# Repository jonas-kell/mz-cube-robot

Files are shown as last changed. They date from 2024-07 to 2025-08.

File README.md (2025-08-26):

# Mathezirkel-Cube-Solving-Robot

https://github.com/user-attachments/assets/eca1f05e-32c8-4683-82ac-e17c1d3a330d

<table style="width: 100%; border-collapse: collapse; border: none;">
    <tr>
        <td style="text-align: center; vertical-align: middle;">
            <video src='files/VideoDemonstration.mp4' controls loop autoplay style="max-width: 45vw; max-height: 80vh;"></video>
        </td>
        <td style="text-align: center; vertical-align: middle;">
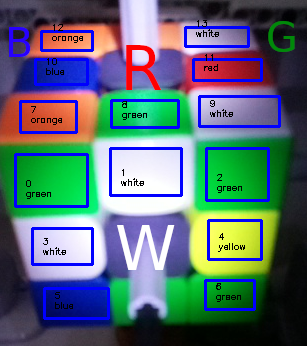
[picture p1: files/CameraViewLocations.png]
            
        </td>
    </tr>
</table>
  
## What is this

This is a Project, undertaken first at the `Mathecamp` of the `University of Augsburg` 2024.
The idea is to

-   Develop a Robot from scratch, that can solve the `Rubics-Cube` without external inputs
-   Make this experience as teachable as possible for young students, that might or might not have been working with robotics/coding yet

## How is this realized

A first version was made to work in September 2024. Videos of the Results can be seen above ([or HERE](https://github.com/user-attachments/assets/eca1f05e-32c8-4683-82ac-e17c1d3a330d)).

The code and Hardware-Setup that is needed to get this working is fully contained in this repository.

There is a list of materials and how to do the basic setup [here](/setup-configuration/bill-of-materials.md).

A Lego-building instruction however is NOT contained here. Though the video can be taken as reference.

Basically, he robot is comprised of a `Raspberry-Pi Zero W` with a camera module.
It provides the stream of the camera view over a simple webserver.
It also relays motor commands to two `Lego Ev3` bricks, that control in total 6 motors, one for each face of the cube.

The `Raspberry-Pi Zero W` has its Wireless capabilities configured as an access point.
One can then connect to that access point and run code one ones own Laptop that processes the camera stream and issues the rotation commands, until the cube is solved.

## What to find in this repository

-   [Bill of Materials](setup-configuration/bill-of-materials.md)
-   [Hardware configuration](setup-configuration/hardware-configuration.md)
-   [Installation instructions](setup-configuration/installation-instructions.md)
-   [Startup instructions for when everything is installed](setup-configuration/startup.md)
-   [Server code to run on the Raspberry Pi](rpi-server.py)
-   [Server code to run on the EV3s](ev3-server.py)
-   [A possible set of processing and issuing functions](solving-example-code/)

## Gallery

The photos are also found at their respective locations in the sub-modules of the explanation above.

<table style="width: 100%; border-collapse: collapse; border: none;">
    <tr>
        <td style="text-align: center; vertical-align: middle;">
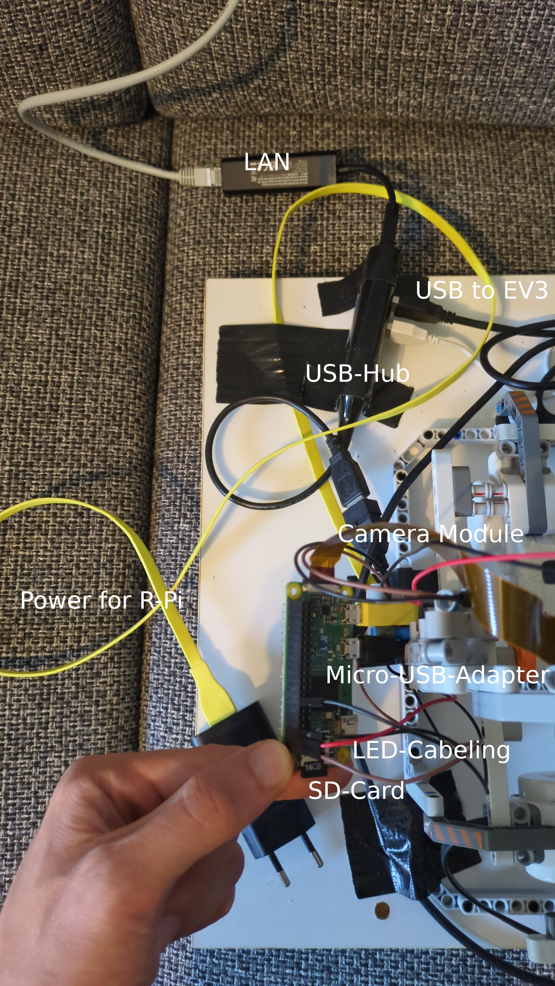
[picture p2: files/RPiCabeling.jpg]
            
        </td>
        <td style="text-align: center; vertical-align: middle;">
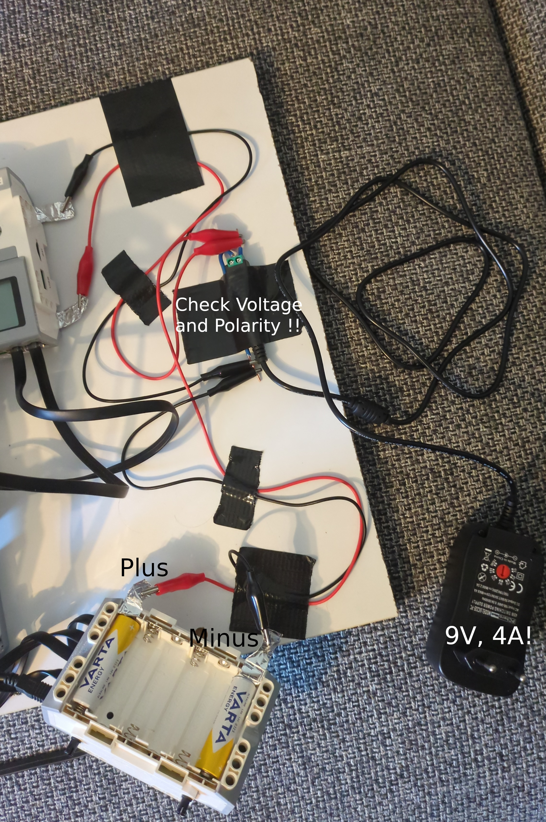
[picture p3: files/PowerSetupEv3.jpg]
            
        </td>
    </tr>
</table>
<table style="width: 100%; border-collapse: collapse; border: none;">
    <tr>
        <td style="text-align: center; vertical-align: middle;">
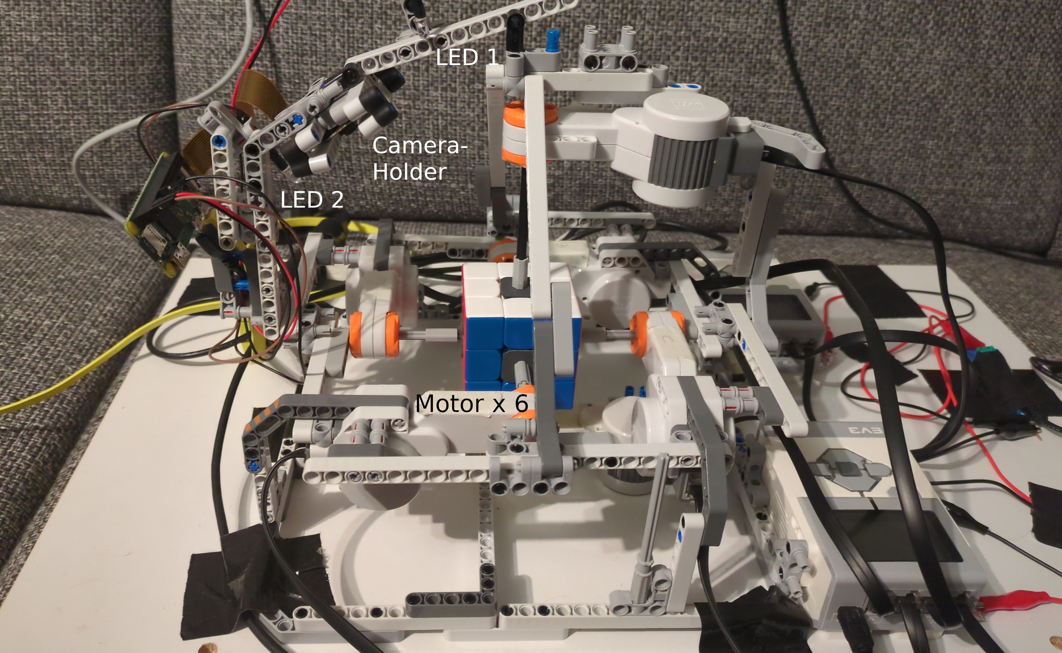
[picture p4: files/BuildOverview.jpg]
            
        </td>
    </tr>
</table>
<table style="width: 100%; border-collapse: collapse; border: none;">
    <tr>
        <td style="text-align: center; vertical-align: middle;">
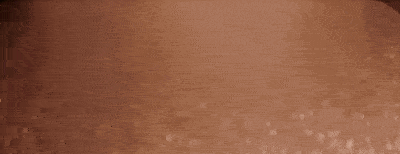
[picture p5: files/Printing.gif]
            
        </td>
        <td style="text-align: center; vertical-align: middle;">
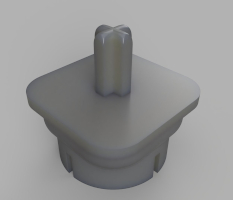
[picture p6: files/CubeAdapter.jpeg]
            
        </td>
    </tr>
</table>

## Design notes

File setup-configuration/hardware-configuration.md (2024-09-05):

# Hardware Configuration

How to setup the hardware:

## Raspberry Pi Setup

-   Connect the Power-Port with the Micro-USB Cable to the 5V Power-Supply
-   Connect the Data-Port to the Micro-USB to USB-A-female Adapter and plug the USB-Hub into this.
    -   Into this, you plug the USB-A sides of the cables that lead to the `Lego EV3`s
    -   Optional: USB-A to ethernet adapter to have LAN-Connectivity to the contraption
-   Get the LEDs to shine with the resistor and the jumper wires (breadboards or soldering required) ([Tutorial](https://www.elektronik-kompendium.de/sites/raspberry-pi/2102181.htm))
    -   [Pinout of the raspberry pi zero](https://pinout.xyz/pinout/io_pi_zero)
        -   I used 2,4 for one side and 6,14 for the other (check polarity of LED)
-   Flash the OS to one of the micro SD-Cards
    -   [Tutorial, to follow for Camera Setup](https://www.conrad.de/de/ratgeber/schule-unterricht/raspberry-pi/ueberwachungskamera-mit-raspberry-pi.html)
    -   [Flashing Program: Raspberry Pi Imager](https://www.raspberrypi.com/software/)
        -   When Flashing the os, make sure to `enable ssh` and set password to `pi`
        -   [Which OS?](https://www.raspberrypi.com/software/operating-systems/)
            -   Raspberry Pi OS (other)
                -   Raspberry Pi OS (Legacy - 32 bit) Lite
    -   Insert into the SD-Card Slot
-   Connect the camera module to the raspberry Pi Zero

## EV3 Setup (Both completely the same)

-   Power Management
    -   Either load with 6AA batteries each
    -   OR connect 9V Wall brick to the power terminals
        -   best to get a connection to the terminal, by wedging Aluminum-Foil/Tinfoil onto the contacts with one AA battery
            -   (the battery just has the correct size, will not be part of the circuit, may also be an empty one)
            -   Check Polarity and which terminal to use
            -   Best to use a Multimeter to check Voltage (9V) and Polarity (see image)
            -   Power supply should provide 4A, lower specs may result in the brick shutting down under load
-   Flash the [ev3dev](https://www.ev3dev.org/docs/getting-started/) onto the remaining two SD-Cards
    -   Can also use Raspberry Pi Imager for this task
    -   Insert the SD-Cards into the `Lego EV3` slot
-   Connect the USB-Cables to the USB-Hub (keep the connection, generally the same configuration. Swapping them may break the assignment in the Network Manager, later)
-   Build your Model (Requires your creativity and a lot of Lego-Parts)
    -   Your freedom of design choice.
        -   Should connect one motor to every face of the cube
        -   Motors should spin freely, the cube nicely in the center
            -   Probably best, to have opposite face motors on the same ev3, as they turn together posssibly
            -   I chose the configuration (See directions on picture below):
                -   A - Blue - Motor Port A, EV3 1
                -   B - Green - Motor Port B, EV3 1
                -   C - Orange - Motor Port C, EV3 1
                -   D - Red - Motor Port D, EV3 1
                -   E - White - Motor Port A, EV3 2
                -   F - Yellow - Motor Port A, EV3 2
        -   Space for the camera to view at least two sides of the cube (the more you can easily see, the easier the detection)
        -   Mount the LEDs, so that they can be powered and still illuminate the cube faces nicely

<table style="width: 100%; border-collapse: collapse; border: none;">
    <tr>
        <td style="text-align: center; vertical-align: middle;">
            
        </td>
        <td style="text-align: center; vertical-align: middle;">
            
        </td>
    </tr>
</table>
<table style="width: 100%; border-collapse: collapse; border: none;">
    <tr>
        <td style="text-align: center; vertical-align: middle;">
            
        </td>
    </tr>
</table>

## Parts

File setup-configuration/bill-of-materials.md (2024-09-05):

# Bill of Materials

What is required to reproduce this setup

-   Two `Lego EV3` ([Discontinued](https://www.lego.com/de-lu/product/lego-mindstorms-ev3-31313), go to ebay)
    -   Six Motors (When you have two EV3, you get 4 large and 2 small motors. The small ones have a different speed though. I happen to have 6 `Lego NXT 2.0 - Motors`).
-   One `Raspberry Pi Zero W` (Zero 2 probably also works and is more performant) [Like this](https://www.reichelt.de/raspberry-pi-zero-w-v-1-1-1-ghz-512-mb-ram-wlan-bt-rasp-pi-zero-w-p256438.html)
    -   `Camera Module` for the Raspberry Pi [Like this](https://www.reichelt.de/raspberry-pi-kamera-8mp-67-v2-rasp-cam-2-p170853.html)
    -   `Pi Zero compatible Adapter Flex Cable` (smaller pins on one side!!) [Like this](https://www.reichelt.de/raspberry-pi-zero-flexkabel-fuer-standard-kameramodul-15cm-rpiz-cam-fl15-p223615.html)
-   Three `16 Gb Micro-SD-Cards` (One for the RPi, one for each of the two EV3)
-   One `Micro USB to USB-A female Adapter` ([Like this](https://www.reichelt.de/de/de/raspberry-pi-kabel-micro-usb-m-auf-usb-typ-a-f-otg-10cm--rpi-usb-b-a-1-wt-p316284.html))
-   One `USB-A USB-Hub` (ideally powered) ([Like this](https://www.reichelt.de/usb-2-0-4-port-hub-4x-a-equip-128955-p311104.html))
-   One `Micro USB to USB-A cable` to power the Raspberry Pi ([Like this](https://www.reichelt.de/usb-2-0-kabel-a-stecker-auf-micro-b-stecker-3-m-shvp-77183-w-p211162.html))
    -   USB-A power brick (Basically any does) ([Like this](https://www.reichelt.de/usb-ladegeraet-5-v-1000-ma-schwarz-goobay-44947-p265655.html))
-   For the LED-Lighting
    -   2x (or more) White LEDs ([Like these](https://www.reichelt.de/led-5-mm-bedrahtet-kaltweiss-18000-mcd-15--led-5-18000-ws-p76715.html))
    -   Cables to solder and connect ([Like these](https://www.reichelt.de/entwicklerboards-steckbrueckenkabel-40-pole-m-m-40-cm-debo-kabelset22-p340347.html))
    -   2x 100 Ohm Resistor (To avoid burning out the LED, when connected to 5V of Pi Zero, [LED Calculator](https://www.digikey.de/de/resources/conversion-calculators/conversion-calculator-led-series-resistor)) ([Like these](https://www.reichelt.de/widerstand-metalloxyd-100-ohm-0207-1-0-w-5--1w-100-p1777.html))
-   If you want to power the `Lego EV3` over Wall power (not feed it 100s of batteries)
    -   Wall power supply, that does 9-10V ([Like this](https://www.amazon.de/dp/B0CCV95BSF))
    -   Alligator Clips ([Like these](https://www.amazon.de/dp/B0D7V5G3WT))
    -   4 Batteries, Tinfoil
    -   Some wire parts, pliers, soldering iron and stuff for connecting them
-   A Rubics-Cube that can have the center caps removed ([This one probably fits the printed adapters](https://speedcubeshop.com/products/moyu-rs3-m-2020-3x3-magnetic))

    -   6 Adapters to connect the YOUR Rubics-Cube centers to Lego-Axles (3d-Printing required or other alternative you fancy, e.g. some hardening putty or what do I know)
    -   [.stl File of the Adapter Model used](./../files/CubeAdapter.stl). Thanks to [@jangeiger](https://github.com/jangeiger) for designing and printing :-)

        Printing &nbsp;&nbsp;&nbsp;&nbsp;&nbsp;&nbsp;&nbsp;&nbsp;&nbsp; Adapter

## Legacy/Alternatives

this project was initially envisioned to be working with one `Lego EV3` and one `Lego NXT 2.0`.
Alternatively two `Lego NXT 2.0`.

The problem is, that one of either `Lego EV3` or `Lego NXT 2.0` doesn't have enough motor-ports for controlling 6 motors.

There is a non-complete version for using `Lego NXT 2.0`.
For one, an old version of the server scripts can be found in the history: [COMMIT](https://github.com/jonas-kell/mz-cube-robot/blob/22c137ebf0f76d9267865a2a87c0837d4efc5210/rpi-server.py).

Also configuration files and other resources are in [this legacy folder](../testing-preparation-setup/nxt-slave/).

This was scrapped due to not solvable motor precision errors when using `Lego NXT 2.0`.

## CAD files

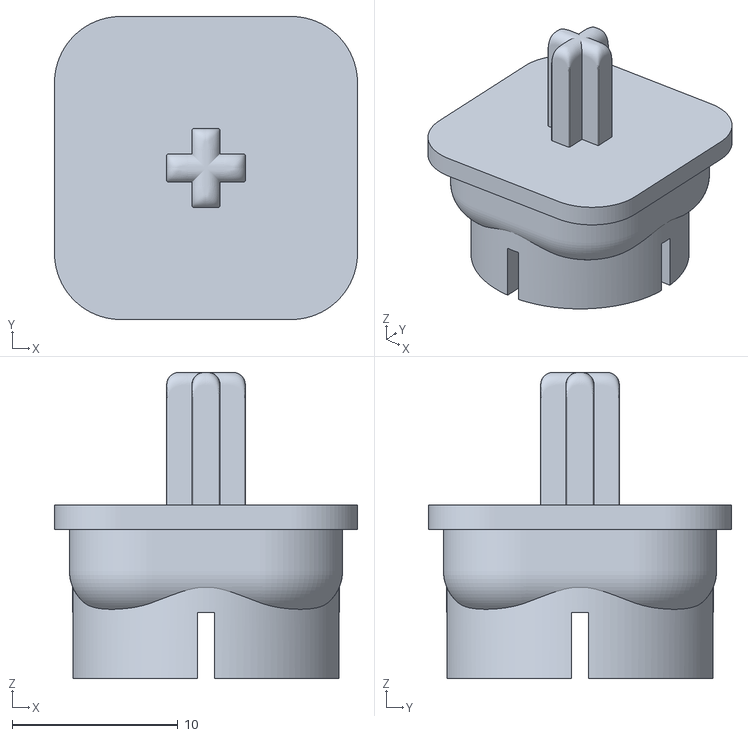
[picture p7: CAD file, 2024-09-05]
files/CubeAdapter.stl
18.3 x 18.3 x 18.5

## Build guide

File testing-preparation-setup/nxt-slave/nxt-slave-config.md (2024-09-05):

# Legacy: talk to NXT2.0

[Last commit, where this was used](https://github.com/jonas-kell/mz-cube-robot/blob/22c137ebf0f76d9267865a2a87c0837d4efc5210/rpi-server.py).

This was scrapped due to not solvable motor precision errors when using `Lego NXT 2.0`.

```shell
# required installations on the raspberry pi zero w to get the nxt-communication package to work
pip install --upgrade pip
pip install --upgrade nxt-python
pip install --upgrade pyusb
```

It was tried, to make this run on the `Lego EV3`, as it has a USB-Host port and could control the `Lego NXT 2.0`.
This was however unsuccessful, to the python version in [ev3dev](https://www.ev3dev.org/) and the requirement for the control pip lib [nxt-python](https://github.com/schodet/nxt-python).

Therefor, the `Raspberry Pi Zero W` was chosen to issue the commands to the `Lego NXT 2.0`.

-   [Main test](discover.py)

Direct Control (running motors commands directly over USB) is way to imprecise.
This is because the device reading the motor encoder and issuing start/stop is incapable to do so effectively due to the USB-delay.

-   [Direct Control EV3](ev3_slave.py)
-   [Direct Control NXT](nxt_slave.py)

The "solution" that reduced that problem, was to run code locally on the `Lego NXT 2.0` that turns the motors and only communicate the direction/speed/amount over serial communication, eliminating the inaccuracy.

The programs were written in [Open Roberta Lab](https://lab.open-roberta.org/), as this is a nice - still supported - way to program the legacy `Lego NXT 2.0`.

The setup how to talk to the robot was under the `Open Roberta Wiki` under `»Set Up«`. This has moved to a confluence site with required login, since, so I refuse to write down links to the details now...

The programs that used the bluetooth communication api to read the message how far and which motor to turn are [Here](./messagemotor.xml).
Attempts were made, to [run motors in parallel](./messagemotorparallel.xml) that were fully unsuccessful.

[Some example how to write messages (text/numbers)](./message.py) to the `Lego NXT 2.0`.

[This server implementation](https://github.com/jonas-kell/mz-cube-robot/blob/22c137ebf0f76d9267865a2a87c0837d4efc5210/rpi-server.py) used a second message channel that was checked for message box empty-nes, because writing messages back into the box from nxt was unsuccessful and so this was the only way I fond to communicate back to the server that we are done.

## END

In the end still motor positioning of any of these was not sufficiently precise enough for repeated use in the final application.

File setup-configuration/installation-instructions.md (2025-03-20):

# Installation Instructions

## On the HOST-Computer (Laptop or whatever processes the image stream and sends the commands)

-   Install the [VS-code ev3-dev extension](https://marketplace.visualstudio.com/items?itemName=ev3dev.ev3dev-browser) if you want to interface directly with the ev3s (like for uploading files, when no network configuration up, yet).
-   Install the [VS-code Python extension](https://marketplace.visualstudio.com/items?itemName=ms-python.python)
-   Python Extensions (in a proper `venv`, not globally):

    ```shell
    python3 -m venv .venv
    source .venv/bin/activate

    pip install --upgrade pip
    pip install --upgrade python-ev3dev2
    pip install --upgrade opencv-python
    pip install --upgrade scikit-image
    pip install --upgrade RubikTwoPhase

    ------ to deactivate
    deactivate
    ```

## On the `Raspberry Pi Zero W`

-   When Flashing the os, MAKE SURE to `enable ssh` and set password to `pi` (otherwise, you will not be able to connect to it, if you do not happen o have the proper HDMI-accessories)
-   Source code initially taken from the [official PiCamera package](http://picamera.readthedocs.io/en/latest/recipes2.html#web-streaming)
-   Make sure, the files are copied onto the devices
    -   [rpi-server](./../rpi-server.py) onto the Raspberry PI with the top level folder `mz-cube-robot`
-   Enable Camera Support

    ```shell
    sudo raspi-config
    ```

    -   Interface Options
        -   Legacy Camera support
            -   Enable
    -   RESTART

-   Install packages

    ```
    sudo apt install python3-picamera
    export PATH="/home/pi/.local/lib/python3.9/site-packages:$PATH"

    # to solve on the pi
    sudo apt-get install python3-opencv
    sudo apt-get install python3-skimage
    sudo pip3 install --upgrade RubikTwoPhase --default-timeout=100

    ```

-   Make the wlan interface be an Access-Point to connect to

    -   Settings to generate a Access-Point with `SSID = CUBEROBOTWLAN` and `Password = cuberobot`

        -   In that network, the `Raspberry Pi Zero W` will have the ip `192.168.1.1`, meaning, the website will be available under [http://192.168.1.1/](http://192.168.1.1/)

    -   Install Packages

    ```shell
    sudo apt install dnsmasq hostapd iptables
    ```

    -   Edit the configuration

    ```shell
    sudo nano /etc/dhcpcd.conf

    >>>>>

    interface wlan0
    static ip_address=192.168.1.1/24
    nohook wpa_supplicant
    ```

    ```shell
    sudo mv /etc/dnsmasq.conf /etc/dnsmasq.conf_alt
    sudo nano /etc/dnsmasq.conf

    >>>>>

    # DHCP-Server active for WLAN-Interface
    interface=wlan0
    # DHCP-Server not active for other networks
    no-dhcp-interface=eth0
    # IPv4-Address-Range and Lease-Time
    dhcp-range=192.168.1.100,192.168.1.200,255.255.255.0,24h
    # DNS - We
    dhcp-option=option:dns-server,192.168.1.1
    ```

    ```shell
    sudo nano /etc/hostapd/hostapd.conf

    >>>>>

    ### WLAN-Access-Point-Mode

    # Interface and driver
    interface=wlan0
    # driver=nl80211 # Commented out, may be necessary

    # WLAN-Configuration
    ssid=CUBEROBOTWLAN
    channel=1
    hw_mode=g
    ieee80211n=1
    ieee80211d=1
    country_code=DE
    wmm_enabled=1

    # WLAN-Encryption
    auth_algs=1
    wpa=2
    wpa_key_mgmt=WPA-PSK
    rsn_pairwise=CCMP
    wpa_passphrase=cuberobot
    ```

    ```shell
    sudo nano /etc/default/hostapd

    >>>>>

    RUN_DAEMON=yes
    DAEMON_CONF="/etc/hostapd/hostapd.conf"
    ```

    -   Start Service (Probably best to also reboot and see if it still works)
        -   !!! If you broke network config, you may no longer be able to connect to the device at all

    ```shell
    sudo systemctl unmask hostapd
    sudo systemctl start hostapd
    sudo systemctl enable hostapd
    ```

-   (Optional) Set the program to autostart:

    ```shell
    sudo nano /etc/systemd/system/controlserver.service
    ```

    ```conf
    [Unit]
    Description=Cube solver control server
    After=network.target

    [Service]
    User=root
    WorkingDirectory=/home/pi/mz-cube-robot
    ExecStart=/usr/bin/python3 /home/pi/mz-cube-robot/rpi-server.py
    Restart=always

    [Install]
    WantedBy=multi-user.target
    ```

    ```shell
    sudo systemctl daemon-reload
    sudo systemctl enable controlserver.service
    sudo systemctl start controlserver.service

    sudo systemctl status controlserver.service
    ```

## On the `Lego EV3`

-   Program-wise everything should work out of the box, no extra installations required.
    -   All necessary run-times should be bundled in ev3 dev.
-   Make sure, the files are copied onto the devices
    -   [ev3-server](./../ev3-server.py) onto both ev3s with the top level folder `mz-cube-robot`
-   Further network configuration below (as it requires interaction between multiple machines)

-   (Optional) Set the programs to autostart:

    ```shell
    sudo nano /etc/systemd/system/ev3server.service
    ```

    ```conf
    [Unit]
    Description=EV3 motor command server
    After=network.target

    [Service]
    User=root
    WorkingDirectory=/home/robot/mz-cube-robot
    ExecStart=/usr/bin/python3 /home/robot/mz-cube-robot/ev3-server.py
    Restart=always

    [Install]
    WantedBy=multi-user.target
    ```

    ```shell
    sudo systemctl daemon-reload
    sudo systemctl enable ev3server.service
    sudo systemctl start ev3server.service

    sudo systemctl status ev3server.service
    ```

## Network configuration (between the `Lego EV3` and the `Raspberry Pi Zero W`)

-   First follow the [connection tutorial](https://www.ev3dev.org/docs/tutorials/connecting-to-the-internet-via-usb/) to get a connection once from your desktop or laptop to the `Lego EV3`s, before you do without a GUI on the `Raspberry Pi Zero W`

    -   We want the `10.42.X.X` subnet. This is hopefully free... (otherwise Google is your friend)
        -   Adapt steps, so that you can connect to both the `Lego EV3`s and they have distinct IPv4 (see below)
    -   Enable `connect automatically`
    -   Preset the IP-Configuration Hardcoded
        -   Go in the connection menu on ev3 to `ipv4 -> load linux defaults`
            -   Now it should be `10.42.0.3` and other settings
        -   Adapt for the second one to
            -   `10.42.1.3` for ipv4
            -   `10.42.1.1` for gateway

-   Read out connections details from your compatible machine.

    ```shell
    sudo cat /etc/NetworkManager/system-connections/ev3dev.nmconnection
    ```

    -   There is an [Example Read out Connection Here](./../testing-preparation-setup/ev3-dev/ev3dev.nmconnection)
        -   The values for your `Lego EV3`s WILL BE DIFFERENT!

-   Now on the `Raspberry Pi Zero W` we can configure the interface

    -   MAC-address must be taken from the just extracted configuration!
    -   CAUTION: ! Only works when connected over lan, because this WILL reset the Access-Point Interface until Restart

    ```shell
    sudo systemctl start NetworkManager
    sudo nmcli # list the connections
    sudo nmcli connection add type ethernet ifname "*" con-name ev3dev ipv4.method shared mac 12:16:53:4A:D7:77 # Adapt to your first EV3s Mac-Address
    sudo nmcli connection add type ethernet ifname "*" con-name ev3dev-2 ipv4.method shared mac 12:16:53:4C:24:3F # Adapt to your second EV3s Mac-Address

    sudo nmcli # list the connections again, now it should be there
    ```

    -   Tell the `Lego EV3`s to reconnect, with static ips assigned
        -   At this point it may be required to swap the USB-Connections to set what will be `usb0` and `usb1`

    ```shell
    sudo ip ad add 10.42.0.1/24 dev usb0
    sudo ip ad add 10.42.1.1/24 dev usb1
    ip addr show usb0
    ip addr show usb1

    # should now have only the 10.42 entry. Delete otherwise the rest with (!! adapt ip and range !!)
    sudo ip addr del 169.254.89.145/16 dev usb0 # adapt preset ip-add/device accordingly
    ```

    -   Test if you can connect to the robot with the static ips we desire

    ```shell
    ssh -o PasswordAuthentication=yes -o PreferredAuthentications=keyboard-interactive,password -o PubkeyAuthentication=no robot@10.42.0.3

        exit

    ssh -o PasswordAuthentication=yes -o PreferredAuthentications=keyboard-interactive,password -o PubkeyAuthentication=no robot@10.42.1.3

        exit
    ```

    -   Now if that works, make it static (currently will get lost on restart)

    ```shell
    sudo ip addr del 10.42.0.1/24 dev usb0 # while still added, cannot live restart the networking because it cannot double assign
    sudo ip addr del 10.42.1.1/24 dev usb1 # while still added, cannot live restart the networking because it cannot double assign
    sudo nano /etc/network/interfaces

    >>>>>

    auto usb0
    iface usb0 inet static
        address 10.42.0.1
        netmask 255.255.255.0

    auto usb1
    iface usb1 inet static
        address 10.42.1.1
        netmask 255.255.255.0

    ```

    -   Perform restart

    ```shell
    sudo systemctl restart networking
    systemctl status networking.service
    ```

    -   Restart everything, now the [Startup Process](startup.md) should be able to be performed

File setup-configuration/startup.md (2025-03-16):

# Startup procedure

## First Time

-   Perform all the steps in [Hardware Setup](./hardware-configuration.md)
-   Perform all the steps in [Installation](./installation-instructions.md)
-   Make sure, the files are copied onto the devices
    -   [ev3-server](./../ev3-server.py) onto both ev3s with the top level folder `mz-cube-robot`
    -   [rpi-server](./../rpi-server.py) onto the Raspberry PI with the top level folder `mz-cube-robot`

## Subsequent Boots

-   Start both `Lego EV3`s FIRST. And wait until they have booted fully (takes some time)
-   THEN start the Raspberry Pi (if started too early, the `Lego EV3`s will not get properly mapped to their network devices)

-   Start the server programs:

    -   If you performed the parts in the manual, that says `(Optional) Set the programs to autostart`, this should NOT be needed
    -   Otherwise: how to start them manually

        -   SSH connections (Perform the commands below in order):
            -   SSH onto pi: default user: `pi`, pw: `pi`
            -   SSH onto ev3 FROM THE PI (only there the USB-Connection is established): default user: `robot`, pw: `maker`

```shell
ssh -o PasswordAuthentication=yes -o PreferredAuthentications=keyboard-interactive,password -o PubkeyAuthentication=no pi@192.168.1.1

    ssh -o PasswordAuthentication=yes -o PreferredAuthentications=keyboard-interactive,password -o PubkeyAuthentication=no robot@10.42.0.3

        sudo python3 ~/mz-cube-robot/ev3-server.py # enter pw, when started abort with ctrl + c
        nohup sudo python3 ~/mz-cube-robot/ev3-server.py &

        exit

    ssh -o PasswordAuthentication=yes -o PreferredAuthentications=keyboard-interactive,password -o PubkeyAuthentication=no robot@10.42.1.3

        sudo python3 ~/mz-cube-robot/ev3-server.py # enter pw, when started abort with ctrl + c
        nohup sudo python3 ~/mz-cube-robot/ev3-server.py &

        exit

    sudo python3 ~/mz-cube-robot/rpi-server.py # enter pw, when started abort with ctrl + c
    nohup sudo python3 ~/mz-cube-robot/rpi-server.py &

    exit
```

This makes sure, that all server programs are running on the devices and the console ssh-connections can be terminated.

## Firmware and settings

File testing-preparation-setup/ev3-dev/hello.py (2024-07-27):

#!/usr/bin/env python3
"""Hello to the world from ev3dev.org"""

import os
import sys
import time

# state constants
ON = True
OFF = False


def debug_print(*args, **kwargs):
    """Print debug messages to stderr.

    This shows up in the output panel in VS Code.
    """
    print(*args, **kwargs, file=sys.stderr)


def reset_console():
    """Resets the console to the default state"""
    print("\x1Bc", end="")


def set_cursor(state):
    """Turn the cursor on or off"""
    if state:
        print("\x1B[?25h", end="")
    else:
        print("\x1B[?25l", end="")


def set_font(name):
    """Sets the console font

    A full list of fonts can be found with `ls /usr/share/consolefonts`
    """
    os.system("setfont " + name)


def main():
    """The main function of our program"""

    # set the console just how we want it
    reset_console()
    set_cursor(OFF)
    set_font("Lat15-Terminus24x12")

    # print something to the screen of the device
    print("Hello World!")

    # print something to the output panel in VS Code
    debug_print("Hello VS Code!")

    # wait a bit so you have time to look at the display before the program
    # exits
    time.sleep(5)


if __name__ == "__main__":
    main()

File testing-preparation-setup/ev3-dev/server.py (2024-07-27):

import socket
from ev3dev2.motor import LargeMotor, OUTPUT_A, SpeedPercent


# url_callback: provided function, that takes the following inputs:
#     the method of the request
#     the url of the request
#
#     and that returns the result-string to be echoed back to the client
def startServer(ipv4, url_callback):
    # HTTP-Server starten
    if ipv4 != "":
        print("Start Server")
        addr = socket.getaddrinfo(ipv4, 80)[0][-1]
        server = socket.socket()
        server.setsockopt(socket.SOL_SOCKET, socket.SO_REUSEADDR, 1)
        server.bind(addr)
        server.listen(1)
        print("Server is listening to ", addr)
        print()
        print("In interactive mode the server can be shut down with CTRL + C")
        print()

    # Auf eingehende Verbindungen hören
    while True:
        try:
            conn, addr = server.accept()
            print("HTTP-Request recieved from Client", addr)
            request = conn.recv(1024)
            request = str(request)
            request = request.split()

            print(request)

            method = request[0].lstrip("'b")
            url = request[1].lstrip("'b")

            print("METHOD:", method)
            print("URL:", url)

            # Process by user defined function:
            resp = url_callback(method, url)

            conn.send(
                bytes("HTTP/1.0 200 OK\r\nContent-type: text/html\r\n\r\n", "utf-8")
            )
            conn.send(bytes(resp, "utf-8"))
            conn.close()

            print("Sent HTTP-Response ")
            print()
        except OSError as e:
            break
        except KeyboardInterrupt:
            break

    try:
        conn.close()
    except NameError:
        pass
    try:
        server.close()
    except NameError:
        pass
    print("Server Exited")


# //TODO more robust version that can decode urlencoded stuff.
# first returns the url_string, then the parameters as object
def parseUrl(url):
    parameters = {}
    url_string = url.split("?")[0] if "?" in url else url
    query_string = url.split("?")[1] if "?" in url else ""

    if query_string:
        pairs = query_string.split("&")
        for pair in pairs:
            key_value = pair.split("=")
            if len(key_value) == 2:
                key = key_value[0]
                value = key_value[1]
                parameters[key] = value

    return url_string, parameters


def test_callback(method, url):
    print(method, url)

    test = LargeMotor(OUTPUT_A)
    test.on_for_rotations(SpeedPercent(100), 1)

    return "success"


startServer("0.0.0.0", test_callback)

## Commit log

2024-07-27 test: motor consistency
2024-07-27 feat: raspi can control both devices
2024-07-27 feat: extract camera stuff from stream
2024-07-28 feat: motor controll
2024-07-28 feat: relay content
2024-07-28 fix: port switch
2024-07-28 feat: nxt proper target interface
    [messagemotor.xml, messagemotorparallel.xml]
2024-07-28 feat: communication nxt motor
2024-07-28 chore: latest nxt program
    [messagemotor.xml]
2024-08-21 fix: motors E and F invert
2024-08-21 fix: breaking but floating motors
    [messagemotor.xml]
2024-08-27 feat: clickable action buttons on home page
2024-08-28 feat: fix shutter speed to counteract led brightness
2024-09-04 fix: motor mapping
2024-09-05 feat: what motor to what
2024-09-05 feat: printing references
    [CubeAdapter.stl]
2025-03-17 feat: on detection fail print how many wrong colors
2025-03-20 feat: print failure
2025-03-20 feat: calibration moves
2025-03-20 feat: switch to calibrated detection
2025-03-20 feat: server side calibration
2025-08-26 fix: stop AB/CD Motors from mixing
